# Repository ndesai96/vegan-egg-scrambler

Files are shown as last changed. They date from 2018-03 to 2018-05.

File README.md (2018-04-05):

# vegan-egg-scrambler
Controls to automate vegan egg scrambling for ME 366J (senior design methodology)

See Fritzing diagram for circuit layout

Hardware components:
- HC-SR04 proximity sensor
- AMG8833 IR camera
- 16x2 LCD display
- INA169 current sensor
- L298N motor controller
- RS-775 12V DC motor
- uxcell 12V 50 RPM geared DC motor

Once downloaded, navigate to File > Preferences within the Arduino IDE and change sketchbook location to the downloaded folder

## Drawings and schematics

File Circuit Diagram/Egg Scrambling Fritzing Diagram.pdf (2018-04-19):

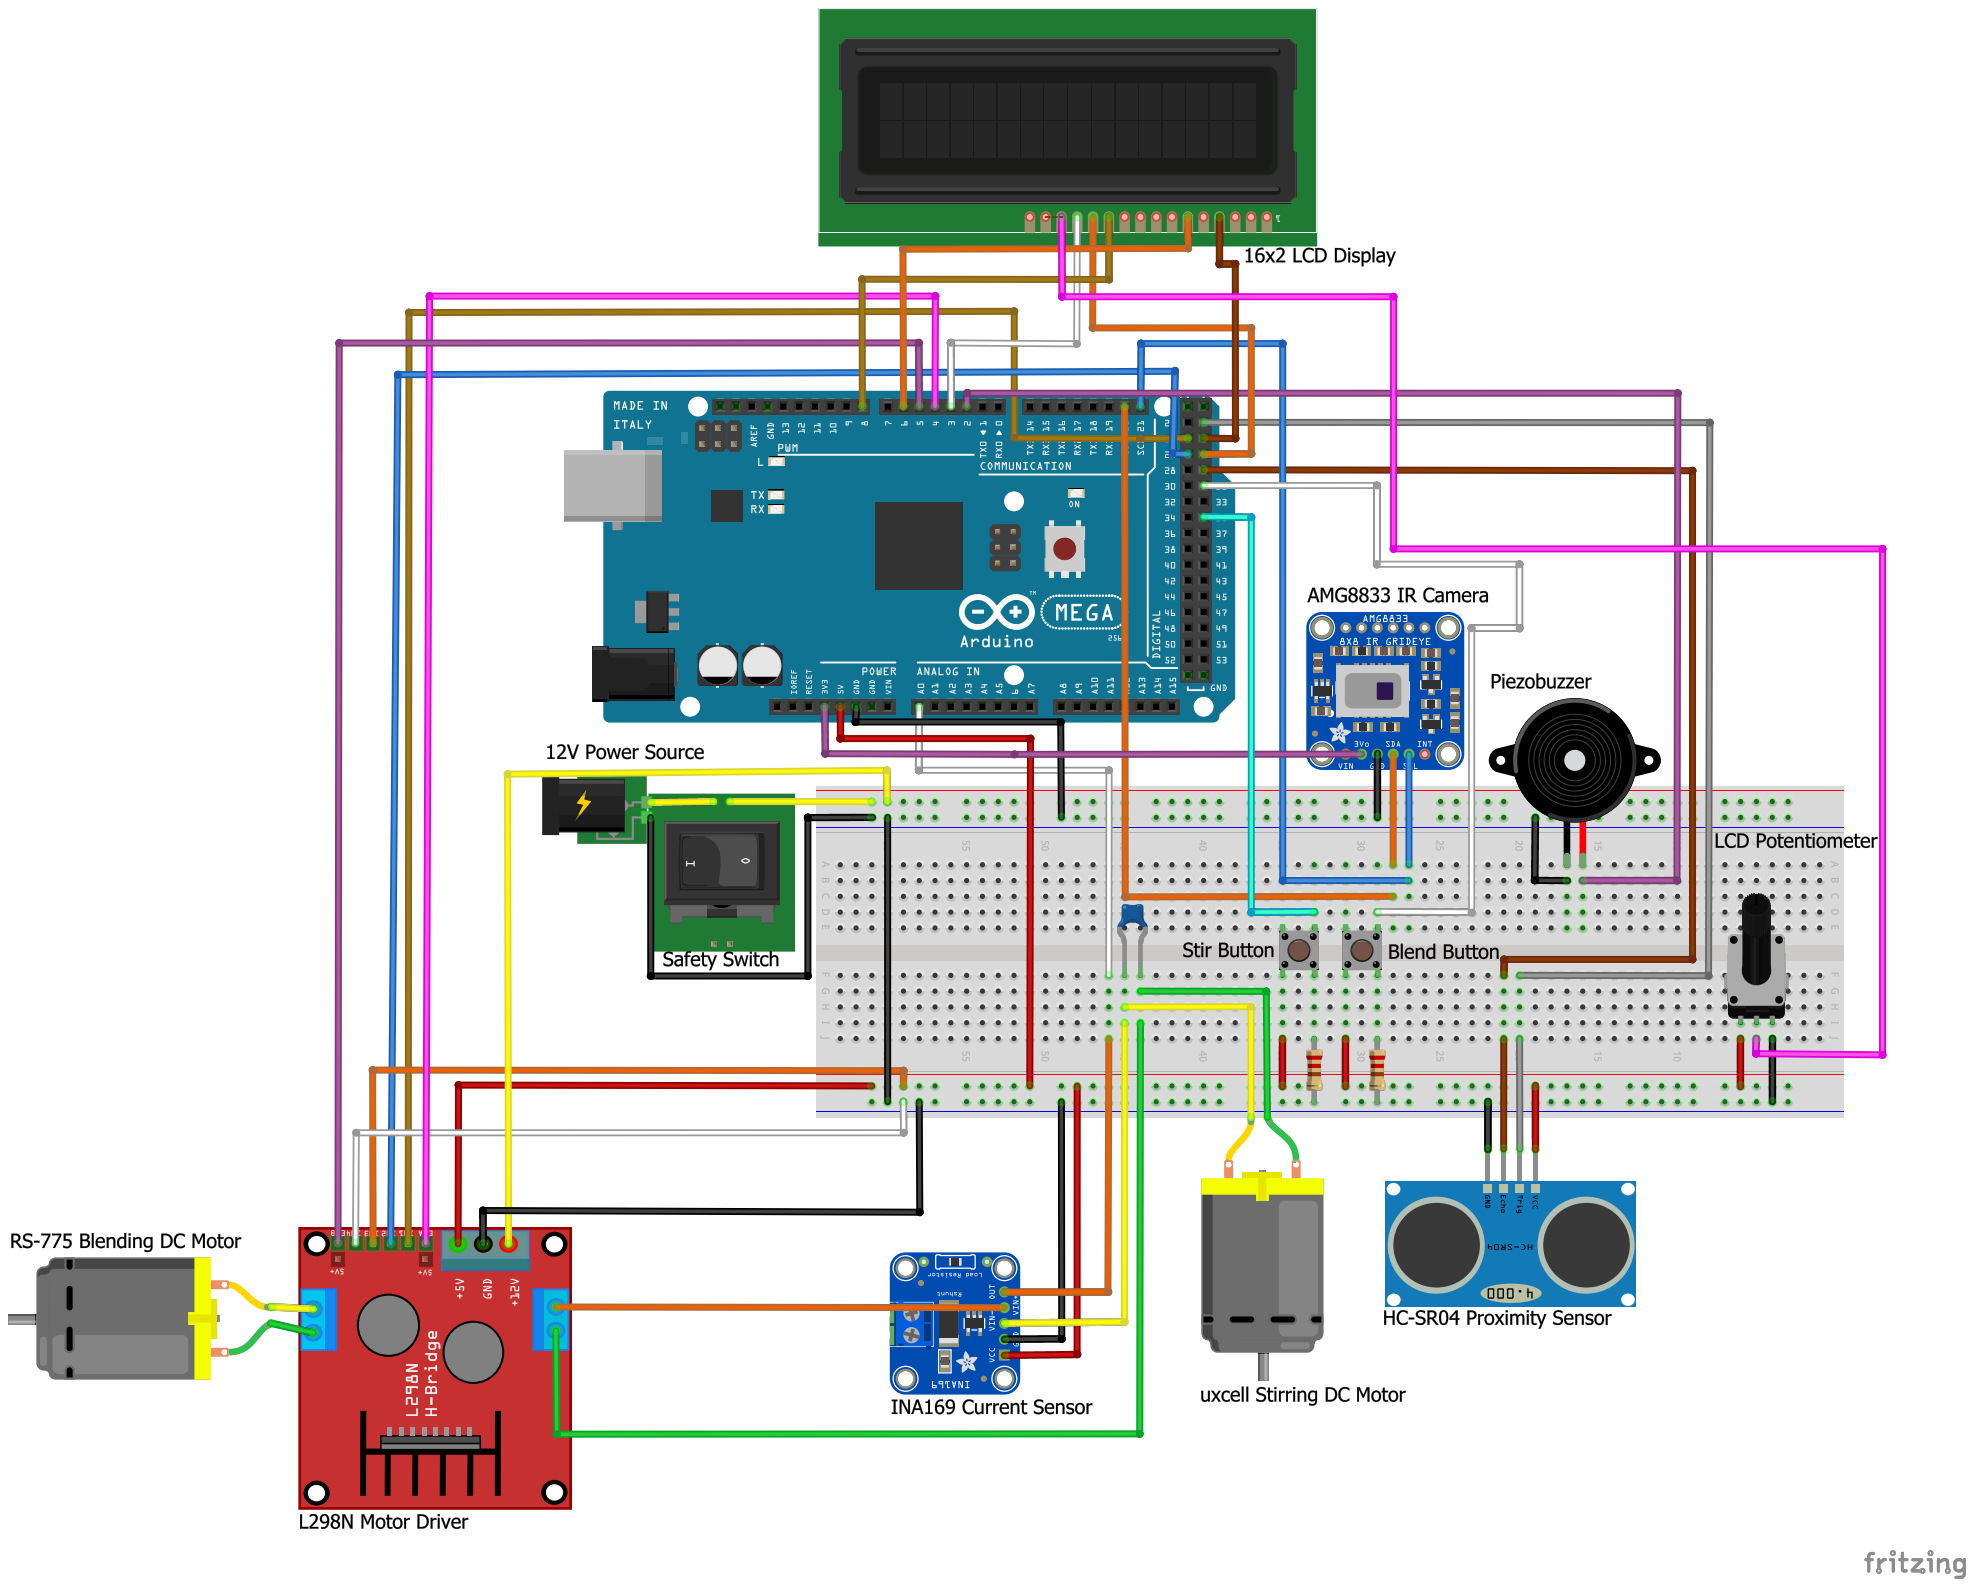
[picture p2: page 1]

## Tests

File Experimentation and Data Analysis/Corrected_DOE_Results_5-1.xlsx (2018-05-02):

Configuration |  |  |  |  |  |  | Data Set 1 |  |  |  |  |  |  |  |  | Data Set2 |  |  |  |  |  |  |  |  | Cook Rate (g/s) |  |  | Transient Heating Rate (°C/s) |  |  | Cook rate g/s |  |  |  |  |  |  | Resulting 2x2 relationship
Trial | Delay | Water | Propeller | d12 | d13 | d23 | Trial | Full jar (g) | Empty Jar (g) | Container (g) | Egg Weight (g) | Water Loss (g) | Transient Heating Rate (°C/s) | Cook Time (s) | Cook rate g/s | Trial | Full jar (g) | Empty Jar (g) | Container (g) | Egg Weight (g) | Water Loss (g) | Transient Heating Rate (°C/s) | Cook Time (s) | Cook rate g/s | Avg. | Variance | S.D. | Avg. | Variance | S.D. | delay vs water |  | delay vs propeller |  | water vs propeller |  |  | Cook Rate (g/s)
1 | -1 | -1 | -1 | 1 | 1 | 1 | 1 | 513 | 256 | 77 | 247 | 87 | 0.359 | 619.596 | 0.140 | 1 | 512 | 268 | 25 | 210 | 59 | 0.380 | 446.148 | 0.132 | 0.1363285942 | 3.338232731e-05 | 0.005777744137 | 0.36969 | 0.0002125922 | 0.01458054183 | Mean response | 0.1318850153 | Mean response | 0.1318850153 | mean response | 0.1318850153 |  | delay vs water = | 0.1319 | + | -0.0056 | x1 | + | -0.0021 | x2 | + | 0.0059 | x1x2
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

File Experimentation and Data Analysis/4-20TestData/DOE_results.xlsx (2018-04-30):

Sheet: Unaltered Data
Before Measurements
toast | g | 25
pb&j | g | 26
sid | g | 77
jar | g | 237
 |  |  |  |  |  |  |  |  |  | Trial 1 Response |  |  |  |  |  |  |  |  |  | Trial 2 Response |  |  |  |  |  |  |  | Cook Time |  |  | Material Loss |  |  | Average Temperature
Time | Trial | Delay | Water | Propeller | d12 | d13 | d23 | d123 | Full jar (g) | Empty Jar (g) | tupperware | tupperware weight (g) | Egg Weight (g) | Material Loss (g) | Consistency | Final avg Temp | Cook Time (s) | start time | full jar (g) | Empty Jar | tupperware | tupperware weight (g) | Egg Weight | Material Loss | Consistency | Final Avg Temp | Cook Time | average | variance2 | variance | average | variance2 | variance | average | variance2 | variance
2018-04-21 | 1 | -1 | -1 | -1 | 1 | 1 | 1 | -1 | 513 | 256 | sid | 77 | 247 | 87 | 0.27 | 66.39 | 619.596 | 2018-04-12 04:21 | 512 | 268 | toast | 25 | 210 | 59 | 0.26 | 51.66 | 446.148 | 532.872 | 15042.10435 | 122.646257 | 73 | 392 | 19.79898987 | 59.025 | 108.48645 | 10.41568289
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

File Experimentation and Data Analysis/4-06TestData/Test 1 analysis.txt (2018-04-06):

	weigths	80																																																															
current	exponential filter 																																																																
0.01	0.01	25.25	25	26.5	27	27.75	28.5	29.5	27.5	20	27.25	17.5	27.25	30	32.75	34	27.25	25	27	28.5	26.75	30.5	30	28.25	27	26	28	29.25	32.75	31.25	25.25	26.25	28	26.25	28.5	31.75	35	31.25	28	26	27.25	25.25	28	29	31.5	30.75	33.5	30.25	27.5	24	25.5	26.5	27.25	27.5	28.25	27.25	27	23.75	23.5	25.5	27.25	26	26.25	26	25.25
0.01	0.01	25.25	24.5	27	26.75	27.75	28	29	27.75	24	26.25	27.5	27.25	30.75	32.75	30.75	27.75	24.75	27.5	28.25	27	30.5	29.75	28.25	26.75	26	28.5	29	32.5	31	25	25.75	27.75	26.5	28.75	31.75	35.25	31.75	28	26.25	27.75	25.5	28.25	29	31.75	31	33.5	30.25	28.25	23.5	25.25	26.25	27.5	28.25	28.5	27.25	27	23.75	23.75	25.5	26.75	26.5	25.75	26	24.75
0.01	0.01	25	24.75	26.75	26.5	28	28.5	29.25	27.75	24.75	26.25	27.25	27	31	32.75	30.75	27	24.75	27.75	28.5	26.25	30.25	30	28.25	27.5	25.5	28	28.75	32.75	31.5	25.25	25.5	28	26.75	29.5	31.75	35.25	31.75	28	25.75	27.75	25.5	28	29	32	31.25	33.5	30	28	24.25	25.75	27.25	27.5	28	29	27.5	28	23.75	24.25	25	26.75	27	26.25	26.5	25.5
0.01	0.01	25	25.25	26.75	27	28	28.25	29.5	27.25	24.25	26.25	27.75	27	30.25	33.25	30.75	27	25	28	28.25	26.75	30.25	30	28.25	26.5	26.5	28.5	29.25	32.75	31.5	25	25.75	27.5	26.75	29	32	35.5	31.75	28.5	26	27.25	25.25	28.25	29.5	32.25	30.75	33.75	30.5	28.75	23.5	25	26.75	27	28.5	28.75	27.25	27.25	23.5	23.5	24.75	27	27.5	26	26	25.5
0.01	0.01	24.75	25	26.5	27	27.75	28.75	29.25	27.25	24.75	26.75	27.75	27.5	30.75	33	30.5	27.5	24.75	27.5	28.25	26.5	30.5	29.75	28.25	26.75	26.25	28	29.5	33.25	31	25.5	25.25	28.25	26.5	29	32	35.75	32	28.25	26	27.75	25.5	28.75	29.5	31.75	31.25	34	30.5	28.5	24	25.5	26.75	27.25	28.25	28.75	27.5	27.25	24.25	24	24.75	26.75	26.75	26.5	26.5	26.25
0.01	0.01	24.75	25.5	27	26.75	27.25	28.5	29.5	28.25	25	26.5	28	27.75	31	33	30.75	28	25.5	27.75	29	26.75	30.75	29.75	29	27	25.75	28.25	29.5	33.25	31.75	25.25	25.75	28.25	26.5	29.25	32.25	36.25	32.25	28.25	26.25	28.25	25.5	28.5	29.75	32.5	31.25	34	30.5	28	24	25.25	26.75	27.25	28.75	28.5	27.75	27.25	23.5	23.75	25.25	26.5	27	26.5	26.75	25.75
0.01	0.01	25	25	26.75	27	28	28.5	29.75	27.25	25	26.5	27.5	27.5	30.75	33.25	30.75	27.5	25.25	28	28.25	27	30.75	30.5	28.75	26.75	26.25	28.5	29.5	33.25	31.5	25	26	28.25	26.75	29.25	32.25	36	32	28.75	26.25	27.5	25.75	28.25	29.5	32.25	31.5	34.5	30.5	28.5	24.25	25	26.75	27.25	28.25	28.5	28	27.5	24	24	25.25	26.75	27	26.75	26.25	25.75
0.01	0.01	24.75	25.25	27.25	27	27.75	28.25	29.75	27.75	24.75	26	27.5	27.25	30.75	33	30.75	27.5	25.75	28	28.5	26.5	30.75	30	28.25	27.25	25.75	28.75	29.5	33	32	25	25.5	28.25	26.25	29.25	32.5	35.75	32.5	28.5	26.25	28	25.25	28	29.5	32.25	31.25	34.5	30.5	28.5	24	25.5	27	27.5	28.25	28.5	27.25	27.75	23.5	23.5	25.5	26.5	26	26.25	26	25.5
0.01	0.01	24	25.25	26.5	26.75	28.25	28.75	29.75	27.25	24.5	26.25	27.5	27.5	31	33	31	27.5	25.25	28	29	26.5	30.5	30	28.75	27.25	26.25	28.5	30	33.5	32	25	25.75	28.25	26.5	29	32.5	36.25	32.25	28.25	26.25	27.75	25	28.5	29.25	32	31.75	34.5	30	28.25	23.5	25	26.5	27.25	28.75	28.75	28.25	27.5	24.25	23.5	25.25	26.75	26.25	26.25	26	25.75
0.01	0.01	24.75	25.25	27	27.25	28.5	28.75	29.75	27.75	24.5	26.5	27.5	27.5	31	33.25	31	27.75	25.25	28	28.75	27	31	30.25	28.5	27.5	26.25	28.75	30	34	32.5	25.75	25.5	28.25	26	29.5	32.5	36.25	32.75	28.25	26	27.75	25.25	28.75	29.5	32.5	31.75	35	30.25	28.75	23.75	25.25	27.25	27.5	27.75	29	27.5	28	23.5	23.75	24.75	27	26.5	26.25	25.75	25.75
0.01	0.01	24.5	25.5	27	27.25	27.75	28.75	29.5	27.75	25	27	28	28	31	33.5	31	28	25	28	28.75	27	31	30.75	28.25	27.25	26	28.75	30	33.75	32.75	25.75	25.75	28.5	26.5	29.5	32.75	36.5	32.75	29	26	27.75	24.75	28.5	30.25	32.5	32	35	30.5	28.25	23.75	25.5	26.75	27.5	28.5	29	27.75	27.75	22.75	23.25	25	27.25	26.75	26.25	26.25	25.75
0.01	0.01	24.5	25.25	27.25	27.75	28.75	28.5	30	28	24.75	26.25	27.75	27.75	31.25	33.5	31	27.75	25.75	28	28.75	27.25	30.75	30.75	29	27.25	26.25	29.25	30.5	33.75	32.75	25.75	26	28.25	26.5	30	33	37.25	32.75	28.75	26.5	28	25.25	28.75	30.25	33.25	32	35.5	31	28.75	23.75	25.75	26.5	27.25	28.75	29	28	28	23.25	24	25.25	27.25	27	26.75	26.5	26.25
0.01	0.01	24.25	25.25	27	27.25	28.25	28.75	30	27.25	25	26.75	27.75	27.75	31.25	33.25	31.5	28	25.75	27.5	29	26.75	31	30.75	29.25	27	26	28.75	30	34	33.25	25.75	25.75	28.5	26.5	30	33	37	33	29	26.5	28.5	25.5	28.75	30.5	33.25	32	35	31	29.25	23.75	25.75	27.25	27.5	29	29	28	27.25	23.5	23.25	25.75	27	27.5	26.75	26.75	26
0.01	0.01	24.5	25.25	27.5	27	28.25	29	30.5	28.25	25.25	27.5	28	28	31.75	33.25	31.5	28	25.25	28.5	29.25	27.5	31.5	31.5	29.25	27.5	26.25	29	30	34	33	25.75	26	29	26.5	30	33	37	33.25	29	26.75	28.5	25.5	28.25	30.25	33.5	32	35.25	31.25	29	24	26	27.5	27.5	29	29.5	28.5	27.75	23.5	23.75	25.5	27.25	27	26.75	26.25	26
0.01	0.01	25	25	27.5	27.25	28.25	29.25	30.5	28.25	25.25	26.75	28.25	28	31.5	33.5	31.25	28	25.5	28.75	29	27.5	31.5	31.75	29.25	27.5	26.5	29	30.5	34.5	33.25	25.75	26.25	29.25	26.75	30	33.25	37.5	33.5	29.5	26.75	28.5	25.5	28.75	30.75	33.25	32.25	35	31	29.5	23.75	25.75	27.5	27.5	29.25	29	28.5	28	24.25	24.5	26	27.5	26.75	26.5	26.75	26
0.01	0.01	25	25.5	27.25	27.75	28.5	29	30.75	28	25.25	27.25	28.25	28	31.75	34	31.25	28.5	26.25	28.5	29.5	27.25	31.75	31	29	27.75	26.75	29	30.5	34.5	33.5	26.25	26.5	28.5	27	29.75	33.25	37.5	33.75	29.25	26.75	28.5	25	28.75	30.75	33	32.25	35.75	31.75	29	23.75	26	27.5	27.75	28.75	29.75	28.75	28.5	23.75	24	26	27.25	27.25	26.75	27	25.75
0.01	0.01	25	25.25	27.5	27.75	29	29.25	30.5	28.25	24.75	27	28.5	28.25	31.75	34	32.25	28.25	25.5	28.5	29	27.25	31.5	31	28.75	27.5	26.5	29.5	30.75	34.5	32.75	25.75	26.5	29.25	26.5	30.25	33.25	37.75	33.5	29.25	26.25	28.75	25.5	29	30.5	33.75	32.5	36	31.5	29.25	23.5	26	27.25	27.75	29	29.25	28.5	28	23.25	24.25	25.75	27.25	27.25	27	26.75	26.5
0.01	0.01	24.75	25.75	27.75	27.75	28.75	29.25	30.5	28.75	25	27.25	28.25	28.5	31.75	33.75	32	28.75	26	29	29.25	27.5	31.75	31.25	29	27.75	26.5	29.75	30.5	35	32.75	26	26.5	29	26.5	30.25	34	38	33.75	29	26.75	29	26	29.5	31.25	33.75	33	36	32	29.25	24.5	25.25	27.75	28	29.25	29.5	28.5	28.5	23.75	24.25	26.25	28	27.25	27	27	26.25
0.01	0.01	24.5	25.25	27.75	27.25	29.25	29.5	30.75	28.5	25.25	26.75	28.5	28.75	31.5	34	31.75	28.75	26	28.5	29.75	27.5	32	31.25	29.25	27.75	27.25	29.75	31	35.25	33.5	25.75	26.25	28.75	27	31.25	34	38.5	33.75	30	27	28.5	26	29.25	30.75	34	32.75	36.5	31.75	29.5	24	26	27.5	27.75	29.75	29.5	28.5	28.25	24.25	23.75	25.75	27.75	27.5	27.25	27	26.75
0.01	0.01	25.25	26	27.5	27.25	29	29	30.75	28.25	24.75	27.25	28.75	28.75	31.75	34.25	32.25	28.75	26	28.75	30	27.5	32	31.25	29.75	28	27	29.75	31	35.25	33.5	25.75	26.5	29.25	27.25	30.5	34	38.75	34.25	29.75	27	28.75	26.25	29.25	31.5	34	32.75	36.5	32	29.5	24.5	26.25	27.5	28	29.5	30.25	29	28.5	24	24.25	26	27.5	27.25	27	27.75	26.5
0.01	0.01	26	25.75	27.5	27.75	29	30	30.75	28.5	24.75	27.75	28.75	29	32.25	34.25	32.25	29.25	26	29	30	27.5	32.25	31	30	28.25	27.25	29.75	31.25	35.75	33.5	25.5	26.5	29.25	27.25	31.25	34.5	38.75	34.25	29.75	27	28.75	25.5	29.5	31.5	34.5	33	36.75	32.25	30.25	24	26.5	27.75	28.25	29.25	30.25	28.5	28.25	24.5	23.75	26.5	27.75	27.75	27.5	27.5	26.75
0.01	0.01	25.5	25.5	27.75	28	28.5	29.5	30.75	29.25	25.25	27.5	28.5	28.25	32	34.5	32	28.5	25.5	29.25	30	27.75	32.25	31	29.5	28	26.75	29.5	31.25	35.5	33.75	25.5	26.25	29.5	27.75	31	34.25	38.75	34.25	29.25	27	29.5	26	30	31.25	34.25	33	37	32	30	24.25	26	27.75	28	29.5	29.5	29	28.5	23.5	24.25	25.5	28	27.75	27	26.75	26.5
0.01	0.01	24.75	25.75	27.5	27.75	28.75	29.75	31	28.5	25.25	27.5	28.5	29	32	34	32.25	28.75	26	29	30.25	27.75	32	31.75	29.5	28	27.25	30	31.25	35.5	33.75	25.75	26.5	29.5	27.5	31.25	34.5	39.25	34.5	29.75	27.25	29	25.75	29.75	31.5	34.25	33.25	37.5	32.5	29.75	24	26.25	28	28.25	29.75	29.75	29	28.75	24	24.75	26	28.5	27.75	27.25	27.5	26.5
0.01	0.01	24.5	25.25	27.75	28.25	29	29.75	31	28.5	25.25	27.75	28.75	28.5	32.25	34.5	32	29.25	25.75	29	29.75	27.75	32.25	31.5	29.25	28	27	29.75	31.5	35.75	33.5	26	26.5	29.5	27.75	31	34.5	39.25	34.5	29.25	27.25	29	26.25	29.25	31.5	34.75	33.25	37.5	32.75	30.25	25	26.25	27.5	28	29.5	29.75	28.75	29	24.25	24.5	26	28	27.5	27.25	27	26.75
0.01	0.01	25	25	27.75	28	29	30	31.25	28.75	25.25	27.75	28.75	29	32.25	34.5	32.25	29	26	29.25	30.25	27.75	32.25	31.75	29.75	28.25	27.25	30	31.5	35.75	34	25.75	26.5	29.75	27.5	31	35	39.5	34.5	29.75	27.25	29.25	26	29.75	31.5	35	33.5	37.25	32.5	30	24.5	26.25	28.5	28.5	29.75	30.25	28.75	29.25	24	24.25	25.75	28.25	27.75	27.5	27.5	27.25
0.01	0.01	25.25	25.5	28	28	29.25	30	31	28.75	24.75	27.5	28.75	28.75	32.25	34.5	32.75	28.5	26.25	29.5	30	27.75	32.75	31.5	29.5	28	27	30.25	31.75	36	34	25.75	26	30	27.25	31	35.25	39.5	34.75	29.75	27	29	26	30	31.75	35	33.5	37.25	32.75	29.75	24.25	26.25	27.75	28.25	29.75	30.25	29	29	24.5	24.5	26	27.75	27.75	27.75	27.25	26.5
0.01	0.01	24.75	25.75	27.75	28	28.75	30	31.25	28.75	25.5	27.75	29.25	28.75	32.25	34.75	33	29	26.25	29.25	30.25	27.5	32.25	31.75	29.75	28	27.5	30.25	31.25	36	34.25	25.75	26.25	29.75	27.5	31.25	35	39.75	34.75	29.75	27.25	29.25	26.25	29.75	32	35	33.25	37.5	32.5	30.25	24.75	26.25	28.25	28.75	30	30.25	29.25	28.75	24.25	24	25.75	28.25	28	27.75	27.25	26.5
0.01	0.01	25.25	25.5	28.25	28	29	30	31.5	29	25	27.5	28.75	29.25	32	34.5	32.75	29.75	26.25	29.5	30.5	27.75	33	31.75	29.75	28.5	27.25	30	31.5	36	34.5	26	26.25	29.5	27	31.25	35.25	39.5	35	29.75	27.25	29.25	26	30.25	32	35.25	33.25	37.5	32.25	30.25	25	26.75	28.5	28.5	29.75	30	28.75	29.25	23.25	24.75	25.75	27.75	28	27.75	27	26
0.01	0.01	25	25.25	28.25	28	29.25	29.75	31.75	29	25	27.75	29.25	29	32	35	32.5	29	26	29	31	27.75	32.5	31.75	30	28.5	27.25	30.5	31.5	36.25	34.5	25.75	26.5	30	27.5	31	35.5	40	35	30	27.25	29.25	26.25	30.25	32	35.25	33.25	37.5	32.5	30.25	24.25	26	27.75	28.5	30	30	28.75	29.25	24.25	24.75	25.5	28.75	27.75	27.75	27	26.5
0.01	0.01	24.75	25.75	28	28	29.25	30.25	31.5	29	25	27.25	29.5	28.75	32.5	35	33	29	26.5	29.25	30.75	28	33	31.5	30	28.25	27.25	30.25	31.75	36.25	35	26	26.75	29.75	27.5	31.5	35.25	40	35.25	29.75	27.25	29.75	26	29.75	32	35	33.75	37.75	32.75	29.75	24.5	26.25	28.25	28.75	30.25	30.25	28.75	29.25	24	24.25	26.5	28.25	27.75	27.5	27.5	27
0.01	0.01	25	25.5	28	28.25	29.5	29.75	31.5	28.75	25	28	29.25	29.25	32.5	34.75	32.75	29.25	26	29.5	30.25	28	33	31.75	29.75	28	26.75	30.75	31.75	36.5	34.5	26	26.5	29.75	27.5	31.5	35.5	40.5	35	29.75	27.25	29.75	25.75	30	32	35.5	34	38	32.75	30.25	24.25	26.25	28	28.75	30	30.75	28.75	29.25	24.5	24.25	25.75	28.25	28	27.75	27.25	27
0.01	0.01	24.75	25.75	28.25	28	29.5	29.75	31.5	29.25	25.25	28	29.25	29.5	32.5	35	33	29.75	26	29.75	31	27.75	33.25	31.75	30	28.25	27.25	30.25	32	36.75	35	25.75	26.5	29.75	27.25	32	35.75	40.5	35	30.5	27.5	30	26.25	30.5	32.5	35.25	34	37.75	32.75	30.25	24.25	26	28	29.25	30	30.25	29	29.25	24.25	24	25.75	29	27.75	28	27.75	26.75
0.01	0.01	25	25.75	28	28	29.25	30.25	31.25	29	25	28.25	29.5	29	32.25	35	33.25	29.5	26.5	29.5	31.25	28.25	33	32	30	28.25	27.5	31	31.75	36.75	34.75	25.75	26.5	30	27.25	32.25	36	40.75	35	30.25	27.75	29.5	25.75	30.75	32.5	35.75	34	38.25	33.25	30.5	24.25	26.25	28.75	28.75	29.75	30.75	29.5	29.25	23.75	25	26.25	28.25	28	27.75	27.5	27
0.01	0.01	25.25	25.75	28.25	28.5	29.75	30.25	32.25	29.75	25.25	28	29.5	28.75	32.75	35	32.75	29.5	27	29.5	30.5	28.25	33.25	32	30	28.5	27.75	30.75	32.25	37.25	35	26.25	26.75	30	27.75	32	35.75	40.5	35.75	30.25	27.75	30.25	26.5	31	32.5	36.25	34.5	38.5	33.25	30.5	23.75	26.5	28.75	28.5	30.25	30.75	29.75	29.25	24.25	24.5	26.25	28	28	28	27.5	26.5
0.01	0.01	25	25.75	28.5	28	29.25	30.25	31.75	28.75	25	27.75	30	29.25	33	35	33.25	29.5	26.25	30	30.5	28.25	33	32.25	29.75	28.5	27.5	31	32.25	37	35	26.25	26.75	30	27.5	32	36.25	41	35.75	30.5	27.5	30.25	26.25	30.25	32.75	36	34.25	38.5	33.25	30.75	24.25	26.75	28.75	28.75	30.5	31	29.25	29.5	24.25	23.75	26.75	28.5	28.75	28.25	28	27
0.01	0.01	25.75	25.5	27.75	28.5	30	30.5	31.5	29.5	25.5	28.25	29.5	29.25	33	35.5	33.25	29.5	26.25	29.75	31	28.5	33.25	32.5	30.25	29	27.5	31	32.5	37	35	26	26.75	30.25	28.25	32.25	36.75	41	35.75	30.25	27.75	29.75	26	30.5	33	36.5	34.25	38.75	33.25	30.75	24.75	26.5	29	29	30.5	31	29.75	29.75	24	25.5	26	29	28.25	28	28	27.25
0.01	0.01	25	25.75	28.5	28.5	29.75	30.75	31.75	29.5	25.25	28.25	29.75	29.25	33	35.25	33.25	29	25.5	30	31	28.5	33.75	32.75	30.5	28.75	28	31.25	32.5	37.25	35.75	26.5	26.75	30.25	28	32.5	36.25	41.25	36	30.5	27.75	30.25	26.25	31.5	33	36.5	34.75	38.75	33.75	30.75	25	27	29.25	29.25	30.75	31.5	30	30	24	24.75	26.25	29.25	28	28.5	28	27.25
0.01	0.01	25.5	26	28.75	28.75	29.5	30.5	32	29.5	25.5	28.5	29.5	29.75	32.75	35.5	33.75	30	26.5	30.5	31.25	28.5	33.5	32.75	30	28.25	27.5	31.25	32.5	37.5	35.5	26.5	26.75	30.25	27.75	32.25	37	41.5	36.5	30.5	28	30.5	26.5	30.75	33	36.25	34.75	39.25	33.5	31.25	25	27	29.5	29.25	30.5	31	29.5	30.25	24.5	24.75	26.25	29	28.5	28.5	28	27.75
0.01	0.01	24.75	26	28.5	28.75	30.25	31	32.25	29.5	25.75	28.5	30	29.25	33.25	35.5	33.75	29.75	26.25	30.75	31.5	28.25	33.75	33	30.25	29	27.5	31.25	32.75	37.75	36	26.25	26.5	30.25	27.75	32.75	36.75	41.5	36.25	31	28	30.25	26.75	31	33	36.5	35	39	33.75	31	24.25	26.75	29.5	29	30.75	31.25	30	29.75	24.5	25.25	26.5	29.25	28.5	28.5	28	27.75
0.01	0.01	25.5	25.75	28.5	29	30	31	32.75	30	25.5	28.25	30	29.5	33	35.75	33.5	29.75	26.25	30.25	31.75	28.75	33.75	32.75	30.25	29	27.75	31.25	32.75	37.5	35.5	26.5	27.5	30.5	28	32.75	37.25	41.5	36.5	31	27.5	30.5	26.25	31	33.5	36.75	35	39.25	34	31	24.5	27	29.5	29	30.5	31.25	30.25	30.5	23.75	24.25	26.25	29	28.25	28.25	28	27.5
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

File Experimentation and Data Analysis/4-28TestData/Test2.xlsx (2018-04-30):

 | 198 |  | IR Camera Pixels
Time | Time (s) | Current | 0 | 1 | 2 | 3 | 4 | 5 | 6 | 7 | 8 | 9 | 10 | 11 | 12 | 13 | 14 | 15 | 16 | 17 | 18 | 19 | 20 | 21 | 22 | 23 | 24 | 25 | 26 | 27 | 28 | 29 | 30 | 31 | 32 | 33 | 34 | 35 | 36 | 37 | 38 | 39 | 40 | 41 | 42 | 43 | 44 | 45 | 46 | 47 | 48 | 49 | 50 | 51 | 52 | 53 | 54 | 55 | 56
0.018 | 18 | 1.36 | 23 | 23 | 20.75 | 20.25 | 26.25 | 26 | 26.25 | 26.5 | 25 | 19 | 18.25 | 18.75 | 20.25 | 22.25 | 24.75 | 26 | 20 | 21.5 | 19.5 | 20.5 | 19.25 | 18.25 | 24.75 | 26.25 | 23.5 | 28 | 28.5 | 21 | 18.25 | 18.5 | 23.5 | 26.5 | 25.5 | 30 | 26.25 | 19.5 | 18.25 | 18.5 | 24.5 | 27 | 21.5 | 25.5 | 22.25 | 19 | 18.75 | 19.25 | 25.25 | 27.25 | 24.75 | 23.75 | 20.25 | 19.25 | 20 | 25 | 25.75 | 26.75 | 27.25
0.628 | 628 | 0.16 | 32.75 | 22.75 | 19.5 | 20.25 | 25.75 | 27.75 | 27.5 | 27.25 | 22 | 19.75 | 19 | 18.5 | 21.75 | 29 | 28.75 | 28.5 | 22 | 20.75 | 19.25 | 19.5 | 29.5 | 31.25 | 29 | 30 | 35 | 27.25 | 25.25 | 27.5 | 40.5 | 38.5 | 28.5 | 32 | 30.75 | 31.25 | 30.5 | 39 | 43.25 | 39.75 | 27.25 | 31.5 | 42.75 | 30.25 | 22.75 | 24.25 | 31.75 | 32 | 28.25 | 31.25 | 39 | 25.25 | 20.75 | 21 | 21.75 | 22.75 | 29.5 | 30.25 | 36
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

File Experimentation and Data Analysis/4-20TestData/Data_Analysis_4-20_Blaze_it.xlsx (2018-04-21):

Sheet: Test3_run1
 |  | IR Camera Pixels
Time | Current | 0 | 1 | 2 | 3 | 4 | 5 | 6 | 7 | 8 | 9 | 10 | 11 | 12 | 13 | 14 | 15 | 16 | 17 | 18 | 19 | 20 | 21 | 22 | 23 | 24 | 25 | 26 | 27 | 28 | 29 | 30 | 31 | 32 | 33 | 34 | 35 | 36 | 37 | 38 | 39 | 40 | 41 | 42 | 43 | 44 | 45 | 46 | 47 | 48 | 49 | 50 | 51 | 52 | 53 | 54 | 55 | 56 | 57
154635 | 1.48 | 27 | 26.75 | 27.25 | 26.75 | 26.5 | 27 | 26 | 25.5 | 26.5 | 26.5 | 27.5 | 26.25 | 26.5 | 27 | 27 | 26 | 26.75 | 26.25 | 27.75 | 26.25 | 26.75 | 26.5 | 26.25 | 26.25 | 27 | 28.75 | 27.75 | 27.5 | 26.5 | 26.25 | 26.75 | 26.75 | 27.75 | 29.5 | 27.75 | 27 | 26.75 | 26.5 | 26.75 | 26.5 | 27.75 | 28 | 27.75 | 26.5 | 27.25 | 26.75 | 27.75 | 27 | 27.5 | 27.75 | 29 | 27.5 | 27 | 27.25 | 27.25 | 27.25 | 28.25 | 27.5
155249 | 0.13 | 26.75 | 26.25 | 26.75 | 27 | 27 | 27 | 26.25 | 26 | 26.75 | 26.25 | 26.25 | 26.75 | 27 | 26.5 | 27.25 | 25.5 | 26.5 | 26.5 | 27 | 27 | 27.25 | 27 | 27.5 | 26.25 | 27 | 26.75 | 28.25 | 28.5 | 28 | 27.5 | 27 | 26.75 | 28 | 29.5 | 28.75 | 28 | 27.75 | 27.75 | 27.75 | 26.5 | 28.5 | 28 | 27.5 | 27 | 27 | 26.75 | 27.75 | 26.75 | 27.75 | 27.5 | 26.75 | 27.5 | 27 | 27 | 27 | 26.75 | 27.75 | 27.5
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

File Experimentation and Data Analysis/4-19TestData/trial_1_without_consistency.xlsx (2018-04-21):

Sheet: Clean Unfiltered Data
74634 | 0 | 56.25 | 59.25 | 54.75 | 61 | 59.25 | 76.5 | 81.25 | 64 | 52.25 | 57.25 | 55.75 | 58 | 69 | 65.75 | 64.5 | 64.25 | 47.5 | 49.75 | 55.25 | 59.75 | 62.5 | 66.25 | 61.5 | 66.5 | 50 | 46.75 | 47.5 | 54 | 60.75 | 53 | 63.25 | 69.25 | 47.75 | 46.75 | 44 | 42 | 42.25 | 50.25 | 65.5 | 68 | 45 | 44.75 | 44.25 | 40.75 | 47.75 | 63.5 | 68 | 66.75 | 47.75 | 45.25 | 46.25 | 44.25 | 52.5 | 66.25 | 68.5 | 67.25 | 55.25 | 56
75243 | 0 | 51.75 | 56.5 | 50.75 | 62.75 | 64.5 | 73.5 | 78.25 | 60.5 | 46.5 | 50 | 49 | 58.5 | 62.25 | 54.75 | 65 | 59.75 | 40 | 41 | 44.5 | 59.75 | 66 | 58.75 | 57.75 | 62 | 45.5 | 46.75 | 47.75 | 56.5 | 57.75 | 62.25 | 58.5 | 65.25 | 44.75 | 46.25 | 47.75 | 54 | 54.75 | 60.75 | 57.75 | 62.25 | 41.25 | 43.75 | 41.5 | 45.75 | 55.25 | 54.75 | 56 | 59.75 | 44 | 41.5 | 40.25 | 45 | 54.25 | 61 | 58.25 | 57.75 | 52 | 53.25
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

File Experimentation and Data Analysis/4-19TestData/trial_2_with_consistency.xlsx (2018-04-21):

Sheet: Clean Unfiltered Data
66178 | 0 | 29.5 | 20.75 | 20.25 | 20.25 | 17.25 | 22.25 | 25.75 | 26.75 | 25 | 22.25 | 20 | 15.5 | 13.5 | 15.75 | 23 | 27.5 | 26.75 | 28 | 26.25 | 14.25 | 13.25 | 17.75 | 31 | 32.5 | 29 | 30.75 | 24.75 | 13.25 | 12 | 17.75 | 25.25 | 38.5 | 29.25 | 32.75 | 20.25 | 12.75 | 12.5 | 13.75 | 21.5 | 40.5 | 26 | 25.75 | 16.25 | 12.5 | 13.25 | 15 | 27.75 | 40.5 | 38.25 | 21.5 | 16.5 | 16.75 | 20.75 | 23.75 | 46.75 | 33.5 | 35 | 31.75
0.09 | 0 | 0 | 0 | 0 | 0 | 0 | 0 | 0 | 0 | 0 | 0 | 0 | 0 | 0 | 0 | 0 | 0 | 0 | 0 | 0 | 0 | 0 | 0 | 0 | 0 | 0 | 0 | 0 | 0 | 0 | 0 | 0 | 0 | 0 | 0 | 0 | 0 | 0 | 0 | 0 | 0 | 0 | 0 | 0 | 0 | 0 | 0 | 0 | 0 | 0 | 0 | 0 | 0 | 0 | 0 | 0 | 0 | 0 | 0
69893 | 0 | 31.25 | 29 | 32.75 | 30 | 27.25 | 29.5 | 32.25 | 32.75 | 30 | 33.25 | 30.5 | 28.5 | 29.5 | 30 | 31.5 | 32.75 | 26.5 | 25.75 | 27.25 | 23.5 | 35 | 35.25 | 30.25 | 33.25 | 29.25 | 31.5 | 29.25 | 23.5 | 25.75 | 26.5 | 24 | 31.75 | 27 | 25.25 | 26 | 22.5 | 27.5 | 31.25 | 27 | 33.25 | 24 | 26 | 25 | 22.75 | 32.75 | 28.5 | 25.25 | 34 | 23.5 | 26.75 | 28.75 | 23.75 | 25.5 | 23.75 | 34.75 | 31.25 | 29.5 | 29.5
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

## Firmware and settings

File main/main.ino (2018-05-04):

#include <Motor.h>
#include <Thermal.h>
#include <Current.h>
#include <LCD.h>
#include <Proximity.h>
#include <Speaker.h>

// Arduino Pins
const int stir_pwm = 3, stir_in1 = 22, stir_in2 = 24, stir_trig = 51;     // stirring motor
const int blend_pwm = 4, blend_in1 = 49, blend_in2 = 47, blend_trig = 53; // blender motor


const int current_sensor = 169, current_data = 0; // current sensor
const int rs = 41, en = 43, d4 = 36, d5 = 38, d6 = 40, d7 = 42; // lcd
const int trig = 23, echo = 25;
const int speaker_pin = 2; 

// Object Initialization
Motor stir(stir_pwm, stir_in1, stir_in2, stir_trig);
Motor blend(blend_pwm, blend_in1, blend_in2,blend_trig);
Current ina(current_sensor, current_data);
LCD lcd(rs, en, d4, d5, d6, d7);
Proximity proximity(trig, echo);
IRCamera amg;
Speaker speaker(speaker_pin);

unsigned long stirStartTime;
unsigned long startTime;

int delayTime = 2000;
int initDelayTime = 5000;


// current sensor parameters
float consistencyThreshold = 0.28;
float unfilCurrent;
int   weight = 60; 
int   crossedConsistencyThreshold = 0;

// binary flags
bool firstLoop = true;
bool firstCycle = true;
bool consistencyDone = false; 
bool tempDone = false;
bool timeOverride = false;
bool interferenceOverride = false; // for proximity sensor

// IR camera parameters
float pixels[AMG88xx_PIXEL_ARRAY_SIZE];
int   pixelLocation[16]= {11,12,13,19,20,21,28,29,36,37,43,44,45,51,52,53}; // array indices
int   tempCounter = 0;
float averageTemp;
float tempThreshold;
  
// progress parameters
int percentConsistency;
int percentTemperature;
int percentTime;
int percentComplete; 

void setup() {
  amg.begin();
  blend.begin();
  proximity.begin();
  speaker.begin();
  lcd.begin(16, 2);
  lcd.clear();
  lcd.setCursor(0,0);
  lcd.print("Ready to Blend");
  Serial.begin(9600); 
}

void loop() {

  // first loop begins/finishes blending and begins stirring
  if (firstLoop) {
    // run blender cycle after user input
   
    blend.waitForTrigger();
    
    blend.runMotor(100);
    lcd.printBlendCountdown(30000);
    blend.stopMotor();

    // notify user that blending is done
    speaker.flatTone(1000, 1500);

    // stir eggs after user input
    stir.waitForTrigger();

    lcd.printStirCountdown(initDelayTime);
    
    stirStartTime = millis();
    stir.primaryDirection();
    stir.runMotor(100);
    firstLoop = false;
  }

  // run stirring in primary direction for 5 seconds
  stir.primaryDirection();
  startTime = millis();
  firstCycle = true;
  while (millis() - startTime < 5000) {

    proximity.handReact(stir, lcd);
    unfilCurrent = ina.getUnfilteredCurrent();
    if ((unfilCurrent > .1) && (unfilCurrent < .4)) {
      ina.setCycleMinMaxCurrent(firstCycle, unfilCurrent);
      firstCycle = false;
    }
    amg.readPixels(pixels);
  
    //Print time, unfiltered current, and temperature array to serial monitor 
    Serial.print((millis()-stirStartTime));
    Serial.print(",");

    Serial.print(unfilCurrent);
    Serial.print(",");
  
    for(int j = 0; j < 64 ; j++){
      Serial.print(pixels[j]);
      Serial.print(",");  
    }
    Serial.println("");
    delay(250); 
  }

  ina.getConsistency(stirStartTime, weight);

  // print consistency to serial monitor
  Serial.print((millis()-stirStartTime));
  Serial.print(",");
  Serial.print(ina.consistency);
  Serial.print(",");
  for(int j = 0; j < 64 ; j++){
    Serial.print("0");
    Serial.print(",");  
  }
  Serial.println("");
  
  // check consistency
  if (consistencyDone == false) {
    
    percentConsistency = min(int((ina.consistency - 0.1) / (consistencyThreshold - 0.1) * 100), 100);
    
    if (ina.consistency >= consistencyThreshold) {
      crossedConsistencyThreshold = crossedConsistencyThreshold + 1;
    }
    if (crossedConsistencyThreshold > 2) {
      consistencyDone = true;
    }
  }

  // CHECK TEMPERATURE
  if (tempDone == false) {
    for (int i =0;i<16;i++) {
       if(pixels[pixelLocation[i]] >= 66) {  // the pixel's temperature value must be greater than or equal 66
         tempCounter = tempCounter + 1;
       } 
    }

    percentTemperature = min(int(tempCounter / 8 * 100), 100);
    
    if(tempCounter >= 8) { 
     tempDone = true;
    }
    else {
      tempCounter = 0;
    }
  }
  
  // CHECK TIME
  if ((millis() - stirStartTime) > 540000) {
    timeOverride = true;
  }
  percentTime = int((millis()-stirStartTime)*100/540000);

  // DISPLAY COMPLETION PERCENTAGE
  percentComplete = max(min(percentConsistency, percentTemperature), percentTime);
  //lcd.printConsistTemp(percentConsistency, percentTemperature);
  lcd.printProgress(percentComplete); 

  // check completion
  if ((tempDone && consistencyDone) || timeOverride) {
    stir.stopMotor();
    // display 100% percent complete message on LCD display
    speaker.texasFight(33);
    lcd.clear();
    lcd.setCursor(0,0);
    lcd.print("Eggs Complete!");
    while (true) {} // infinite loop to delay until reset
  }

  // runs stirring in reverse direction
  stir.reverseDirection();
  startTime = millis();
  while (millis() - startTime < 3000) {
      proximity.handReact(stir, lcd);
    delay(250);
  }
  stir.stopMotor();
  delay(delayTime);
  stir.runMotor(100);

}

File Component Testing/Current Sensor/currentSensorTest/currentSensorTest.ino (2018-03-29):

// USER INPUT

const int analogPin = 0; // analog pin used for current sensor
const int motorPin = 3; // digital pin for motor

int runningAvgCt = 10; // number of values considered in average current calculation
int delayTime = 100; // time between loops in milliseconds

float desiredSpeedPercent = 50; // duty cycle percentage (PWM)

// variable/constant/default initialization;

int raw_value; // container for analogRead value with offset
const float raw_offset = 511.0; // experimentally determined DC offset for current sensor
const float cal_m = 0.727; // calibration coefficient
const float cal_b = 0.0195; // calibration offset

float current; // container for current value
float runningAvg; // container for the averaged current
float currentSum = 0.0; // container for sum of current values
float motorSpeed = 0.0; // container for motor speed output

void setup() {

  // start serial output
  pinMode(motorPin,OUTPUT);
  Serial.begin(9600); // baud rate of 9600
}

void loop() {
  //start motor 
  
  if(motorSpeed>=0 && motorSpeed<=255) {
    analogWrite(motorPin,motorSpeed);
    for (int i = 0; i < runningAvgCt; i++){
      // read and adjust raw value reading from sensor
      raw_value = analogRead(analogPin) - raw_offset;
      current = (raw_value*cal_m) + cal_b;
      currentSum = currentSum + current;
      delay(100);
    }
    runningAvg = currentSum / runningAvgCt;
    Serial.println(runningAvg);
    currentSum=0;
  }
   //code current stop
  if( abs(current)>2.5) { 
    motorSpeed=0;
  }
  else {
    motorSpeed=desiredSpeedPercent*255/100;
  } 
}

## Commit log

2018-03-20 Added folder and file for current sensor test code
2018-03-20 Added folder and file for proximity sensor test code
2018-03-21 Automated offset calculation, adjusted analogPin definition, need to check calibration
2018-03-23 Added Current Calibration Formula
2018-03-27 Running average and current threshold
2018-03-28 Blender motor timer
2018-03-29 Added thermal sensor folder
2018-03-29 Cleaned up hard-coded values, need to add exponential filter
2018-03-29 Added basic proximity sensor test
2018-03-29 Deleted uneccessary Proximity Sensor folder
2018-03-30 Updated proximity sensor tutorial link
2018-04-01 Added current sensor test with motor controller
2018-04-01 Added current sensor code to second test
2018-04-01 Minor change to second current sensor test
2018-04-02 Add exponential filter to original current sensor with new motor
2018-04-03 Drew circuit diagram with Fritzing; added code for IR camera
    [Egg Scrambling Fritzing Diagram.fzz]
2018-04-03 bug fixes; made quick stovetop test code for Claire
    [thermalSensorCLAIRE.ino, thermalSensorTest.ino]
2018-04-03 INA169 sensor code and calibration
2018-04-03 INA169 calibration
2018-04-05 Built library for current sensor class, added/modified libraries for other sensors, fixed readme, and created main function
    [main.ino]
2018-04-05 Removed MegunoLink references and library, implemented own exponential filter
2018-04-05 Updated sensor test with Current library
2018-04-05 Current library modifications and proximity sensor test update (working)
2018-04-06 Added plotter script for pyserial interface; wrote motor class libraries
2018-04-06 Inclusion of motor in main code
    [equipmentCheck.csv, test1.csv]
2018-04-06 Test data
    [test 1 analysis.xlsx, test2.csv, test3.csv]
2018-04-11 Generalized motor library
2018-04-12 Added delay and switch to blender motor
2018-04-12 Simple circuit with switch
2018-04-12 Restored Motor library for general use
2018-04-12 Implement blender motor
2018-04-14 Reorganized experimentation folder; added 4-13 test data
    [config1-propeller-height-changed.csv, config1.csv, config3.csv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]
2018-04-14 Updated Fritzing diagram, updated Motor library to include trigger, reworded Current library slightly, added consistency measurement and thresholding to main, made logic changes to main
    [Egg Scrambling Fritzing Diagram with Mega.fzz, Egg Scrambling Fritzing Diagram.fzz]
2018-04-15 fritzing changes, main debugging
    [Egg Scrambling Fritzing Diagram with Mega.fzz]
2018-04-15 buzzer addition to main code
    [main.ino]
2018-04-16 Fritzing diagram updates
    [Egg Scrambling Fritzing Diagram with Mega.fzz, Egg Scrambling Fritzing Diagram.fzz]
2018-04-18 Added consistency gathering to Current library
2018-04-19 Added speaker library, speaker calls in main, and made slight corrections to motor
    [main.ino, texasFightSong.ino]
2018-04-19 Added motor restart after hand checks
2018-04-21 4-20 testing updates
    [test7_run1.csv, trial3_run1.csv, trial5_run1.csv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]
2018-04-21 Temperature check, pixel location, and test data
    [DOE_results.xlsx, trial_1_without_consistency.xlsx, trial_2_with_consistency.xlsx]
2018-04-21 data anaysis for 4/20 test
    [DOE_results.xlsx, Data_Analysis_4-20_Blaze_it.xlsx]
2018-04-22 File organization and data collection
    [trial1_run1.csv, trial1_run2.csv, trial2_run1.csv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]
2018-04-22 Continued to process experimental data
    [DOE_results.xlsx]
2018-04-22 Standard error calculations
    [DOE_results.xlsx]
2018-04-22 Recalculations for DOE and matlab code to plot
    [DOE_results.xlsx]
2018-04-23 Add normalized temperature and cook rate
    [DOE_results.xlsx]
2018-04-23 Updated surface plots
    [DOE_results.xlsx]
2018-04-24 Steady-state temp analysis
    [DOE_results.xlsx]
2018-04-26 LCD debug and 04-26 testing
    [04-26-Exp1.csv, 04-26-Exp2.csv]
2018-04-27 Steady state temperature graph
    [04-26-Exp2.csv, 04-26-Exp2.xlsx]
2018-04-28 formatting tables for report
    [DOE_results.xlsx]
2018-04-28 4-28 Test 1 added
    [test1.csv]
2018-04-28 added test 2
    [Test2.csv]
2018-04-29 4/28 data analysis updates
    [04-26-Exp2.xlsx, test1.csv, test1.xlsx]
2018-04-30 DOE filtered data
    [DOE_results.xlsx, Test2.csv, Test2.xlsx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]
2018-05-01 Corrected responses for DOE
    [Corrected_DOE_Results_5-1.xlsx]
2018-05-02 Corrected DOE excel aligned with final reoprt
    [Corrected_DOE_Results_5-1.xlsx]
2018-05-04 Updated pins for new wiring
2018-05-04 Updated consistency threshold
    [Final_Test.csv]
